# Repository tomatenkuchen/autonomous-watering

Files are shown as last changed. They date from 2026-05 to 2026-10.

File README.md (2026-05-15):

# autonomous-watering
esp32c6 based, solar powered, battery backuped garden water supply system

## todo
The objective of this project is to have an autonomous-as-can-be field water management system. it supports:
- [ ] multiple 24Vdc water valve connections for water distribution
- [ ] solar power supply to avoid grid wiring
- [ ] battery backup for valve power supply in case no sun is shining. watering is done best after heavy sun hours anyway
- [ ] wifi access point for watering configurations and updates
- [ ] optional conductivity sensor to measure earth humidity
- [ ] maybe maybe wifi powered wether data access to avoid watering just before the storm. GPS data relevant?
- [ ] bonus project: support for an electric fence to have sheep stay away from my salad

## Hardware

can be found in [this](./hw) folder. it's a [kicad](https://www.kicad.org) project, so no worries about licenses.
for now i plan to have an [ESP32C6] as the computing base.

## Software

is found in [this](./sw) folder. as it is an embedded project, it fits the hardware described in the [hardware folder](./hw).

## License

i intent to have the software and hardware licensed for GNU GPLv2. You will find either hardware part libraries or software libraries
licensed under different licenses (duh!), so please check the individual folders and references.

## Liabilities

this is my personal DIY project. It's supposed to be battery backed, so at least no grilling yourself on the grid issues to expected here.
nontheless, electrical danger lurks everywhere. Consider yourself to be warned! If you hurt yourself by soldering stuff, (mis-)handling batteries,
tripping over wires or get struck by lightning while setting up the system outside, blame yourself, not me.

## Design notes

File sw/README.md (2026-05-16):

# firmware for autonomous watering system

since hardware is using an esp32c6 as a controller and access interface for config and more, we need some code to flash onto it.

## usage

connect your pcb to your computer using a usb c cable.

to set up toolchain use:

```bash
pip install conan
conan config install https://github.com/tomatenkuchen/conan-settings.git
conan 

```

to build use:

```bash
source ~/my/path/to/esp-idf/export.sh
conan build . -pr=esp32c6 -b=missing
```

to flash use (after build):

```bash
conan export-pkg . -pr=esp32c6
```

## why conan

i know conan to be a useful package manager that has most of the software onboard that i need to use for my projects

## general structure

the device needs access to the following resources for the device to work properly:
- rtc for time keeping without network
- adc for earth conductivity measurement
- some gpios for valve switching

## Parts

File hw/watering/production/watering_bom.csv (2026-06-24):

Designator | Footprint | Quantity | Value | LCSC Part #
AE1 | Texas_SWRA117D_2.4GHz_Left | 1 | Antenna_Shield
BT1, BT2 | BH-18650-B1BA002 | 2 | 4V3 | C2988620
C1, C2 | 603 | 2 | 15p | C1644
C13, C14, C15, C16, C17, C18, C19, C20, C21, C24 | 603 | 10 | 1u | C15849
C26, C27, C28, C29, C30, C31, C32, C33, C34, C35, C36 | 1206 | 11 | 22u | C12891
C5, C6, C7 | 603 | 3 | 100n | C14663
D3 | TSOT-23 | 1 | D_TVS_Dual_AAC | C32677
D4, D5, D6, D7, D8 | D_SMA | 5 | SS210 | C14996
J2 | USB_C_Receptacle_GCT_USB4105-xx-A_16P_TopMnt_Horizontal | 1 | USB_C_Receptacle | C2927038
J3, J4, J6 | DB142R-5.08-2P-GN | 3 | Conn_01x02_Pin | C2898709
L10, L11, L13, L14, L8, L9 | L_Changjiang_FTC303020D | 6 | 22u | C18724424
Q1 | SOT-23 | 1 | 2N7002 | C8545
R1, R2 | 603 | 2 | 5k1 | C23186
R10, R14, R15, R17, R18, R20, R23, R24, R25, R28, R30, R31, R32, R35, R37, R38, R39, R43, R9 | 603 | 19 | 10k | C25804
R11, R29 | 603 | 2 | 47k | C25819
R12, R41, R42, R5 | 603 | 4 | 1k | C21190
R13, R21, R6 | 603 | 3 | 39k | C23153
R16, R22, R36 | 1206 | 3 | 0R1 | C25334
R19, R26, R40 | 603 | 3 | 100k | C25803
R27 | 603 | 1 | 220k | C22961
R33, R34 | 603 | 2 | 47 | C23182
SC1 | DB142R-5.08-2P-GN | 1 | Solar_Cell | C2898709
SW2, SW3 | SW_SPST_TS-1088-xR020 | 2 | KMS221GLFS | C720477
U1 | QFN-40-1EP_5x5mm_P0.4mm_EP3.6x3.6mm | 1 | ESP32-C6 | C5364646
U10, U8, U9 | SOIC-8_3.9x4.9mm_P1.27mm | 3 | MCP6002-xSN | C7377
U11, U4, U5, U6 | SOT-23-6 | 4 | STI3508 | C708881
U2 | WSON-8-1EP_2x2mm_P0.5mm_EP0.9x1.6mm | 1 | DRV8220DSG | C3681269
U3 | SOIC-8_5.3x5.3mm_P1.27mm | 1 | W25Q128JVS | C97521
U7 | WLCSP-4_0.64x0.64mm_Layout2x2_P0.35mm | 1 | NCP163AFCT330T2G | C603648
Y1 | Crystal_SMD_3225-4Pin_3.2x2.5mm | 1 | 40MHz | C9010
Y2 | Crystal_SMD_3215-2Pin_3.2x1.5mm | 1 | 32768Hz | C32346

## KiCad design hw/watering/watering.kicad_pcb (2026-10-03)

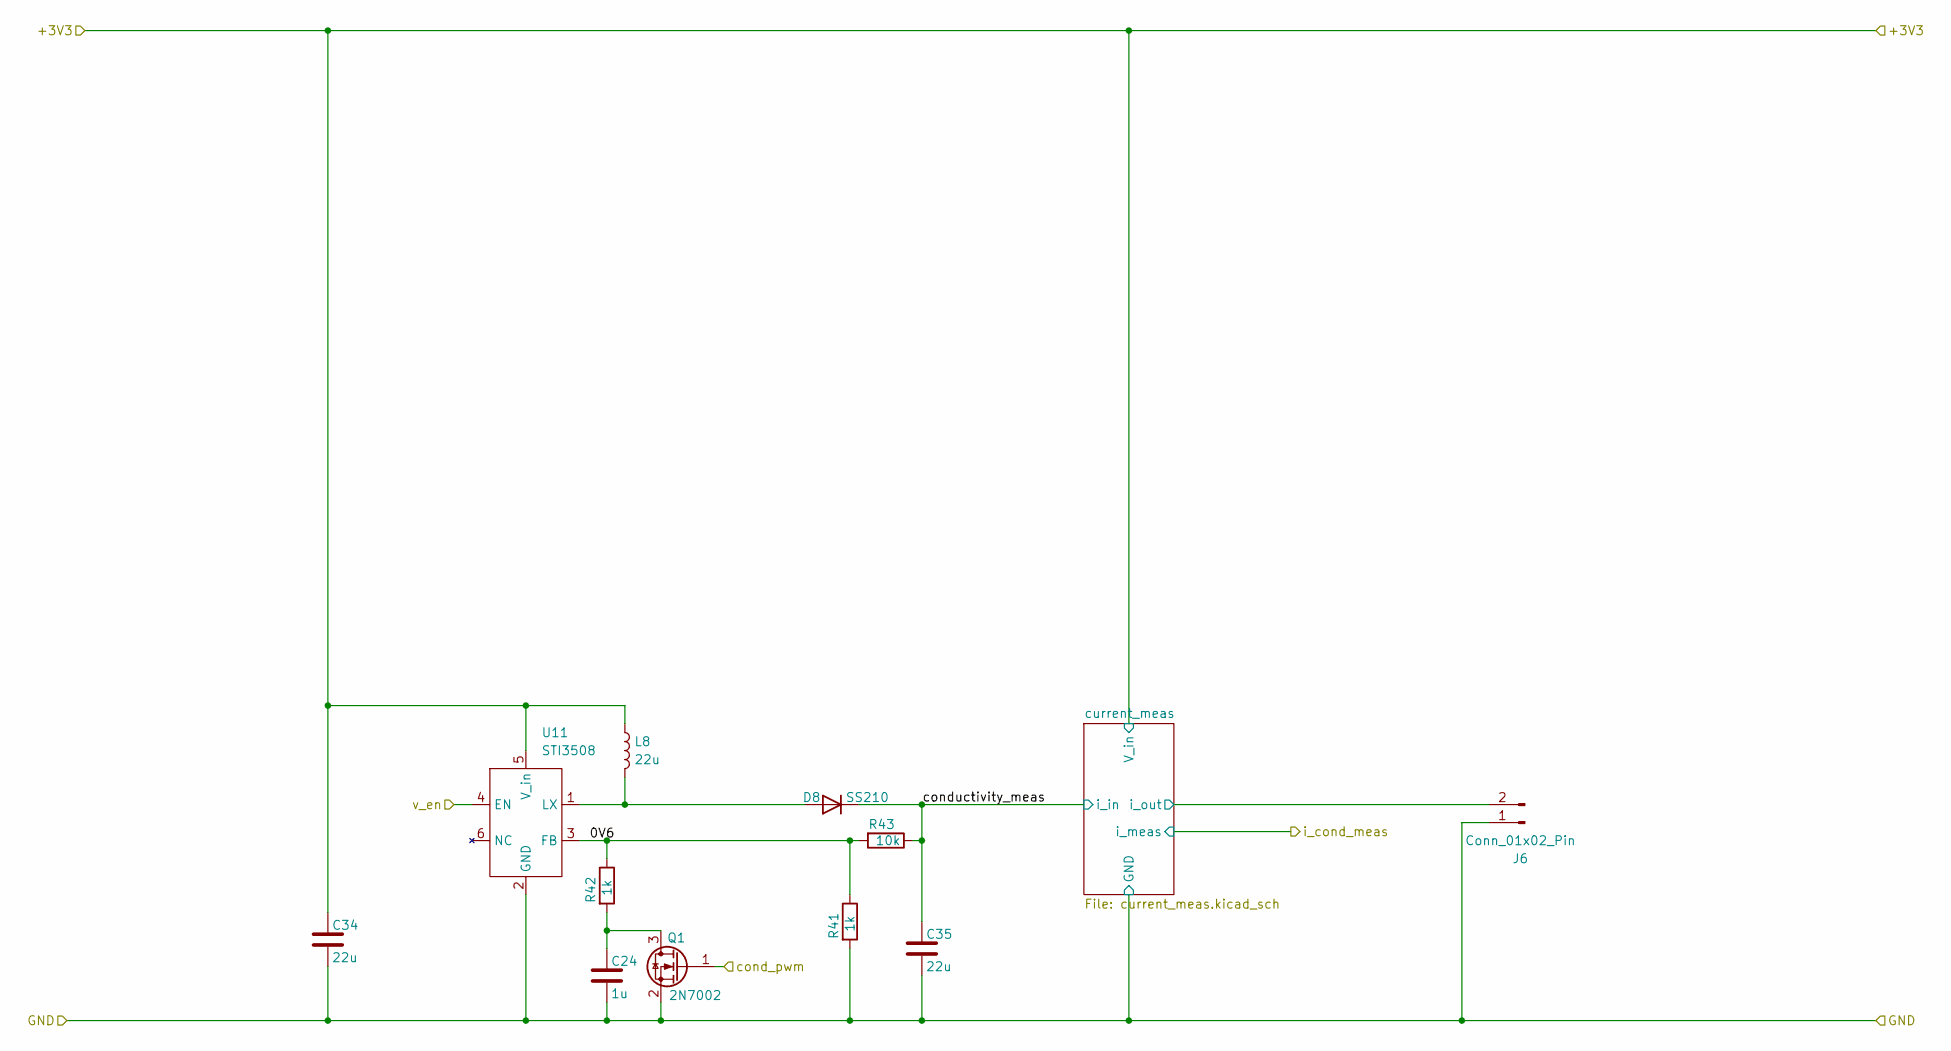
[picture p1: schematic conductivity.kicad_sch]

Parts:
C24: 1u; C_0603_1608Metric
C34, C35: 22u; C_1206_3216Metric
D8: SS210; D_SMA
J6: Conn_01x02_Pin; DB142R-5.08-2P-GN
L8: 22u; L_Changjiang_FTC303020D
Q1: 2N7002; SOT-23
R41, R42: 1k; R_0603_1608Metric
R43: 10k; R_0603_1608Metric
U11: STI3508; SOT-23-6

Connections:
/GND: C24.2, C34.2, C35.2, J6.1, Q1.2 (S), R41.2, U11.2 (GND); also elsewhere on the board
/V_bat: C34.1, L8.1, U11.5 (V_in); also elsewhere on the board
/conductivity/0V6: R41.1, R42.1, R43.2, U11.3 (FB)
/conductivity/cond_pwm: Q1.1 (G); also elsewhere on the board
/conductivity/conductivity_meas: C35.1, D8.1 (K), R43.1; also elsewhere on the board
/conductivity/current_meas/i_out: J6.2; also elsewhere on the board
/conductivity/v_en: U11.4 (EN); also elsewhere on the board
unnamed: D8.2 (A), L8.2, U11.1 (LX)
unnamed: C24.1, Q1.3 (D), R42.2

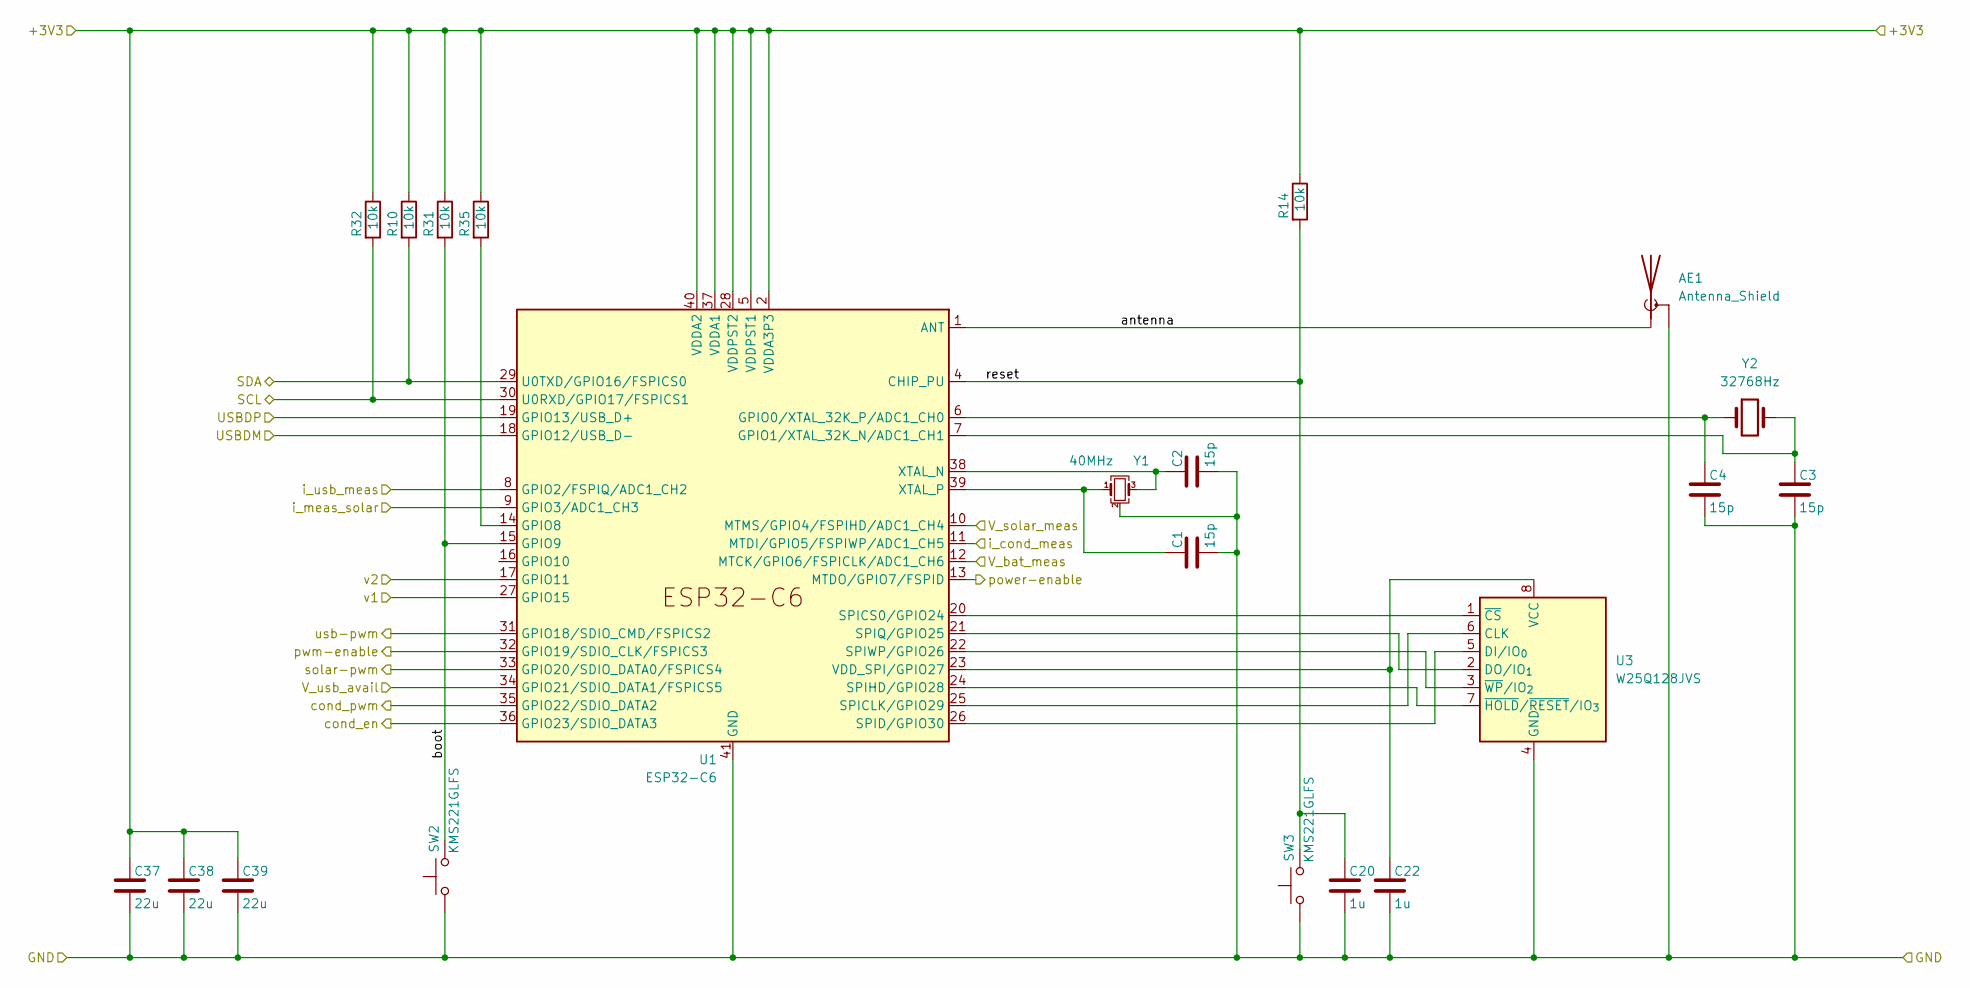
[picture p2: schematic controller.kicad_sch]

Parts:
AE1: Antenna_Shield; Texas_SWRA117D_2.4GHz_Left
C1, C2, C3, C4: 15p; C_0603_1608Metric
C20, C22: 1u; C_0603_1608Metric
C37, C38, C39: 22u; C_1206_3216Metric
R10, R14, R31, R32, R35: 10k; R_0603_1608Metric
SW2, SW3: KMS221GLFS; SW_SPST_TS-1088-xR020
U1: ESP32-C6; QFN-40-1EP_5x5mm_P0.4mm_EP3.6x3.6mm
U3: W25Q128JVS; SOIC-8_5.3x5.3mm_P1.27mm
Y1: 40MHz; Crystal_SMD_3225-4Pin_3.2x2.5mm
Y2: 32768Hz; Crystal_SMD_3215-2Pin_3.2x1.5mm

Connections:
/+3V3: C37.1, C38.1, C39.1, R10.1, R14.1, R31.1, R32.1, R35.1, U1.2 (VDDA3P3), U1.3 (VDDA3P3), U1.5 (VDDPST1), U1.28 (VDDPST2), U1.37 (VDDA1), U1.40 (VDDA2); also elsewhere on the board
/GND: AE1.2 (Shield), C1.2, C2.2, C3.2, C4.2, C20.2, C22.2, C37.2, C38.2, C39.2, SW2.1, SW3.1, U1.41 (GND), U3.4 (GND), Y1.2 (G), Y1.4 (G); also elsewhere on the board
/conductivity/cond_pwm: U1.35 (GPIO22/SDIO_DATA2); also elsewhere on the board
/conductivity/i_cond_meas: U1.11 (MTDI/GPIO5/FSPIWP/ADC1_CH5); also elsewhere on the board
/conductivity/v_en: U1.36 (GPIO23/SDIO_DATA3); also elsewhere on the board
/controller/SCL: R32.2, U1.30 (U0RXD/GPIO17/FSPICS1)
/controller/SDA: R10.2, U1.29 (U0TXD/GPIO16/FSPICS0)
/controller/USBDM: U1.18 (GPIO12/USB_D-); also elsewhere on the board
/controller/USBDP: U1.19 (GPIO13/USB_D+); also elsewhere on the board
/controller/V_bat_meas: U1.12 (MTCK/GPIO6/FSPICLK/ADC1_CH6); also elsewhere on the board
/controller/V_solar_meas: U1.10 (MTMS/GPIO4/FSPIHD/ADC1_CH4); also elsewhere on the board
/controller/V_usb_avail: U1.34 (GPIO21/SDIO_DATA1/FSPICS5); also elsewhere on the board
/controller/antenna: AE1.1 (A), U1.1 (ANT)
/controller/boot: R31.2, SW2.2, U1.15 (GPIO9)
/controller/i_meas_solar: U1.9 (GPIO3/ADC1_CH3); also elsewhere on the board
/controller/i_usb_meas: U1.8 (GPIO2/FSPIQ/ADC1_CH2); also elsewhere on the board
/controller/power-enable: U1.13 (MTDO/GPIO7/FSPID)
/controller/pwm-enable: U1.32 (GPIO19/SDIO_CLK/FSPICS3); also elsewhere on the board
/controller/reset: C20.1, R14.2, SW3.2, U1.4 (CHIP_PU)
/controller/solar-pwm: U1.33 (GPIO20/SDIO_DATA0/FSPICS4); also elsewhere on the board
/controller/usb-pwm: U1.31 (GPIO18/SDIO_CMD/FSPICS2); also elsewhere on the board
/controller/v1: U1.27 (GPIO15); also elsewhere on the board
/controller/v2: U1.17 (GPIO11); also elsewhere on the board
unnamed: C4.1, U1.6 (GPIO0/XTAL_32K_P/ADC1_CH0), Y2.1
unnamed: C3.1, U1.7 (GPIO1/XTAL_32K_N/ADC1_CH1), Y2.2
unnamed: R35.2, U1.14 (GPIO8)
unnamed: U1.25 (SPICLK/GPIO29), U3.6 (CLK)
unnamed: U1.20 (SPICS0/GPIO24), U3.1 (~CS)
unnamed: U1.26 (SPID/GPIO30), U3.5 (DI/IO_{0})
unnamed: U1.24 (SPIHD/GPIO28), U3.7 (~HOLD/~RESET/IO_{3})
unnamed: U1.21 (SPIQ/GPIO25), U3.2 (DO/IO_{1})
unnamed: U1.22 (SPIWP/GPIO26), U3.3 (~WP/IO_{2})
unnamed: C22.1, U1.23 (VDD_SPI/GPIO27), U3.8 (VCC)
unnamed: C2.1, U1.38 (XTAL_N), Y1.3
unnamed: C1.1, U1.39 (XTAL_P), Y1.1

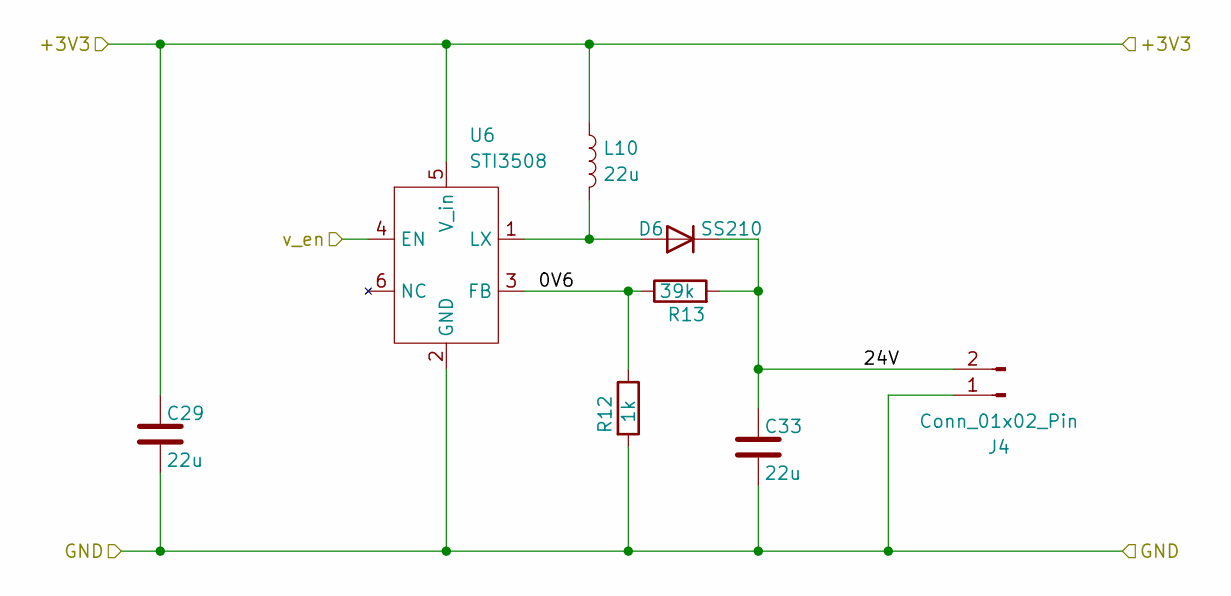
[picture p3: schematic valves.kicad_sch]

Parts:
C29, C33: 22u; C_1206_3216Metric
D6: SS210; D_SMA
J4: Conn_01x02_Pin; DB142R-5.08-2P-GN
L10: 22u; L_Changjiang_FTC303020D
R12: 1k; R_0603_1608Metric
R13: 39k; R_0603_1608Metric
U6: STI3508; SOT-23-6

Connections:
/GND: C29.2, C33.2, J4.1, R12.2, U6.2 (GND); also elsewhere on the board
/V_bat: C29.1, L10.1, U6.5 (V_in); also elsewhere on the board
/controller/v2: U6.4 (EN); also elsewhere on the board
/valves2/0V6: R12.1, R13.1, U6.3 (FB)
/valves2/24V: C33.1, D6.1 (K), J4.2, R13.2
unnamed: D6.2 (A), L10.2, U6.1 (LX)

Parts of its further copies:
C28, C30: 22u; C_1206_3216Metric
D7: SS210; D_SMA
J3: Conn_01x02_Pin; DB142R-5.08-2P-GN
L11: 22u; L_Changjiang_FTC303020D
R5: 1k; R_0603_1608Metric
R6: 39k; R_0603_1608Metric
U4: STI3508; SOT-23-6

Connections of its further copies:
/GND: C28.2, C30.2, J3.1, R5.2, U4.2 (GND); also elsewhere on the board
/V_bat: C28.1, L11.1, U4.5 (V_in); also elsewhere on the board
/controller/v1: U4.4 (EN); also elsewhere on the board
/valves1/0V6: R5.1, R6.1, U4.3 (FB)
/valves1/24V: C30.1, D7.1 (K), J3.2, R6.2
unnamed: D7.2 (A), L11.2, U4.1 (LX)

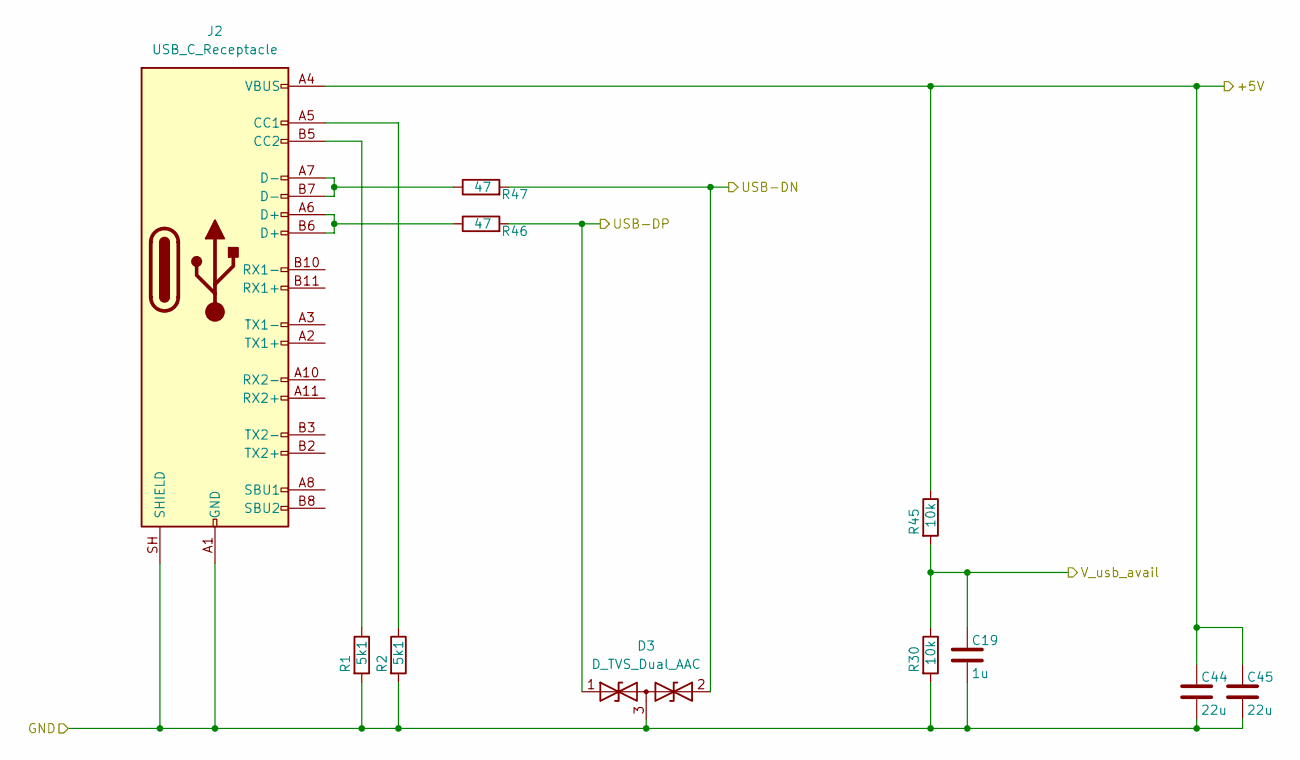
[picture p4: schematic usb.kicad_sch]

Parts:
C19: 1u; C_0603_1608Metric
C44, C45: 22u; C_1206_3216Metric
D3: D_TVS_Dual_AAC; TSOT-23
J2: USB_C_Receptacle; USB_C_Receptacle_GCT_USB4105-xx-A_16P_TopMnt_Horizontal
R1, R2: 5k1; R_0603_1608Metric
R30, R45: 10k; R_0603_1608Metric
R46, R47: 47; R_0603_1608Metric

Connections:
/+5V: C44.1, C45.1, J2.A4 (VBUS), J2.A9 (VBUS), J2.B4 (VBUS), J2.B9 (VBUS), R45.1; also elsewhere on the board
/GND: C19.2, C44.2, C45.2, D3.3 (common), J2.A1 (GND), J2.A12 (GND), J2.B1 (GND), J2.B12 (GND), J2.SH (SHIELD), R1.2, R2.2, R30.2; also elsewhere on the board
/controller/USBDM: D3.2 (A2), R47.2; also elsewhere on the board
/controller/USBDP: D3.1 (A1), R46.2; also elsewhere on the board
/controller/V_usb_avail: C19.1, R30.1, R45.2; also elsewhere on the board
unnamed: J2.A5 (CC1), R2.1
unnamed: J2.B5 (CC2), R1.1
unnamed: J2.A6 (D+), J2.B6 (D+), R46.1
unnamed: J2.A7 (D-), J2.B7 (D-), R47.1

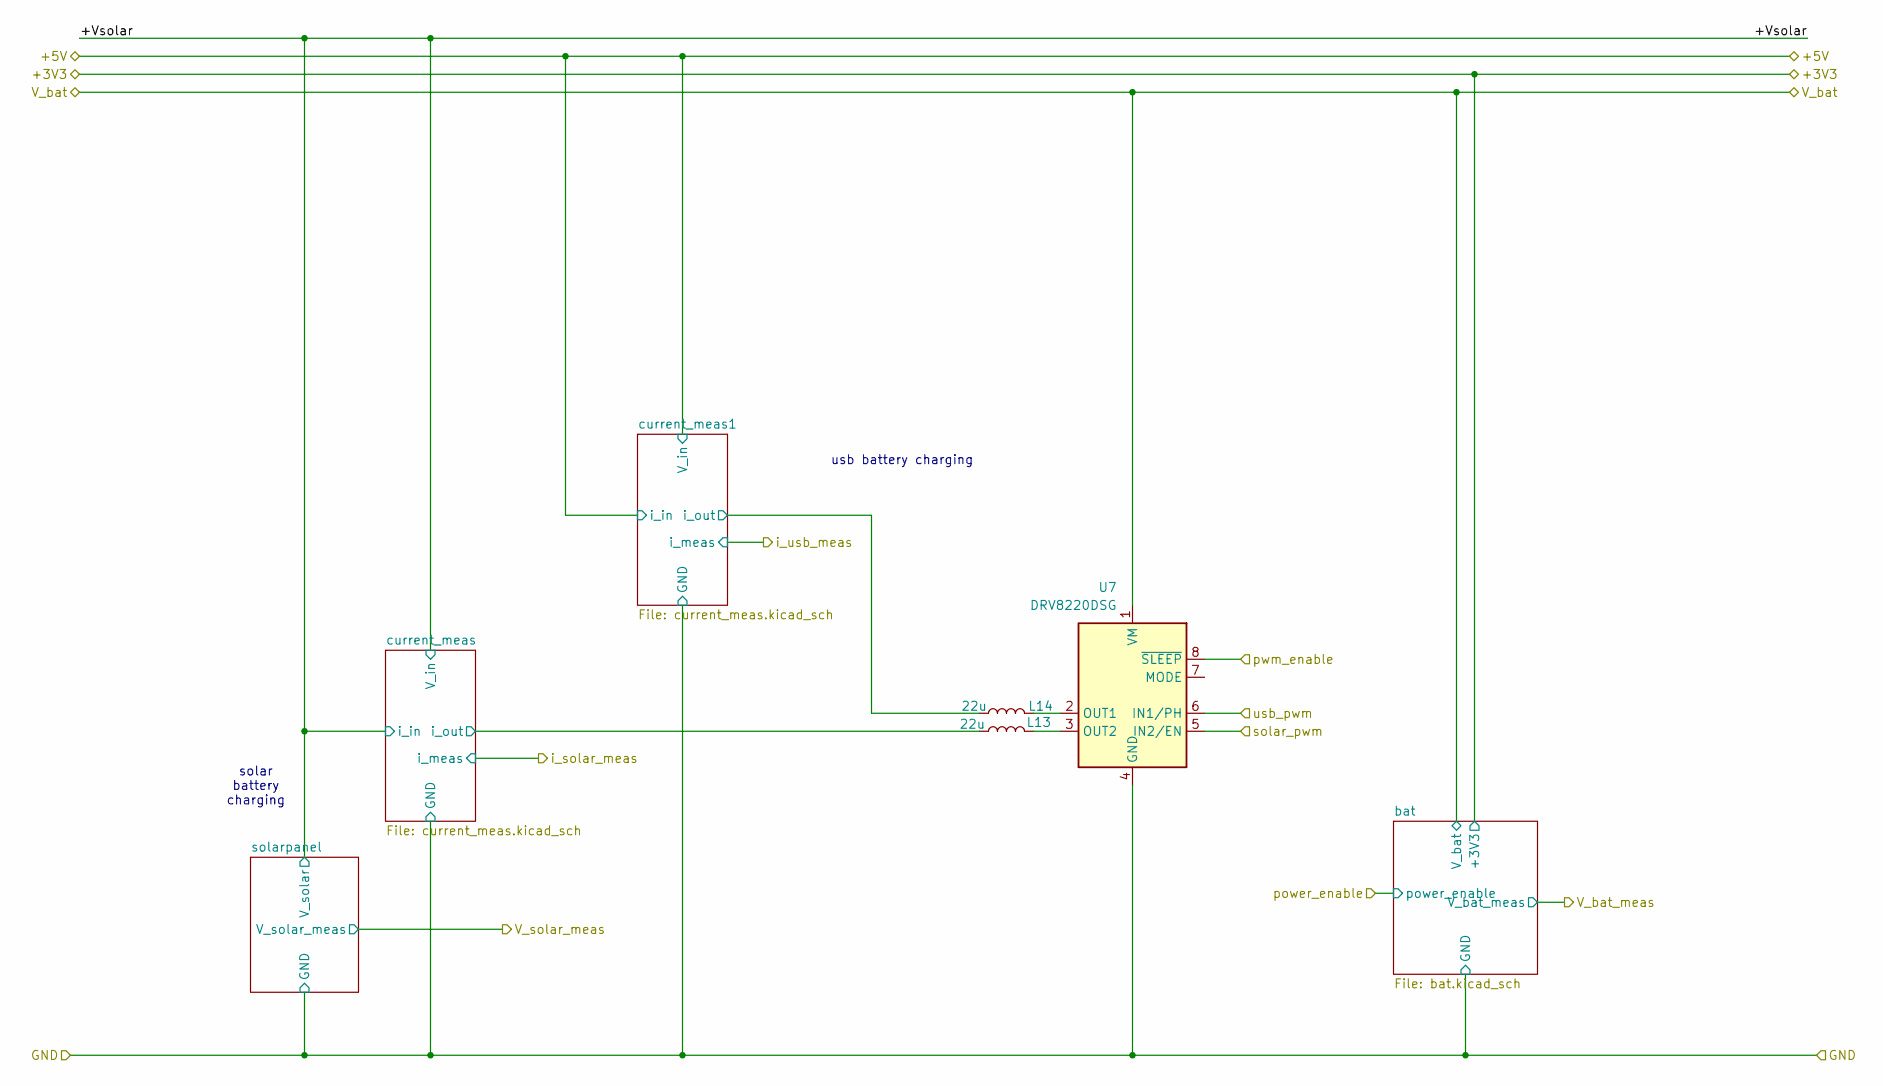
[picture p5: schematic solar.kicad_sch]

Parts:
L13, L14: 22u; L_Changjiang_FTC303020D
U7: DRV8220DSG; Texas_DSG0008A_WSON-8-1EP_2x2mm_P0.5mm_EP0.9x1.6mm

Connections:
/GND: U7.4 (GND), U7.9 (GND); also elsewhere on the board
/V_bat: U7.1 (VM); also elsewhere on the board
/controller/pwm-enable: U7.8 (~SLEEP); also elsewhere on the board
/controller/solar-pwm: U7.5 (IN2/EN); also elsewhere on the board
/controller/usb-pwm: U7.6 (IN1/PH); also elsewhere on the board
/solar/current_meas1/i_out: L14.2; also elsewhere on the board
/solar/current_meas/i_out: L13.2; also elsewhere on the board
unnamed: L14.1, U7.2 (OUT1)
unnamed: L13.1, U7.3 (OUT2)

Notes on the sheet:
usb battery charging
solar battery charging

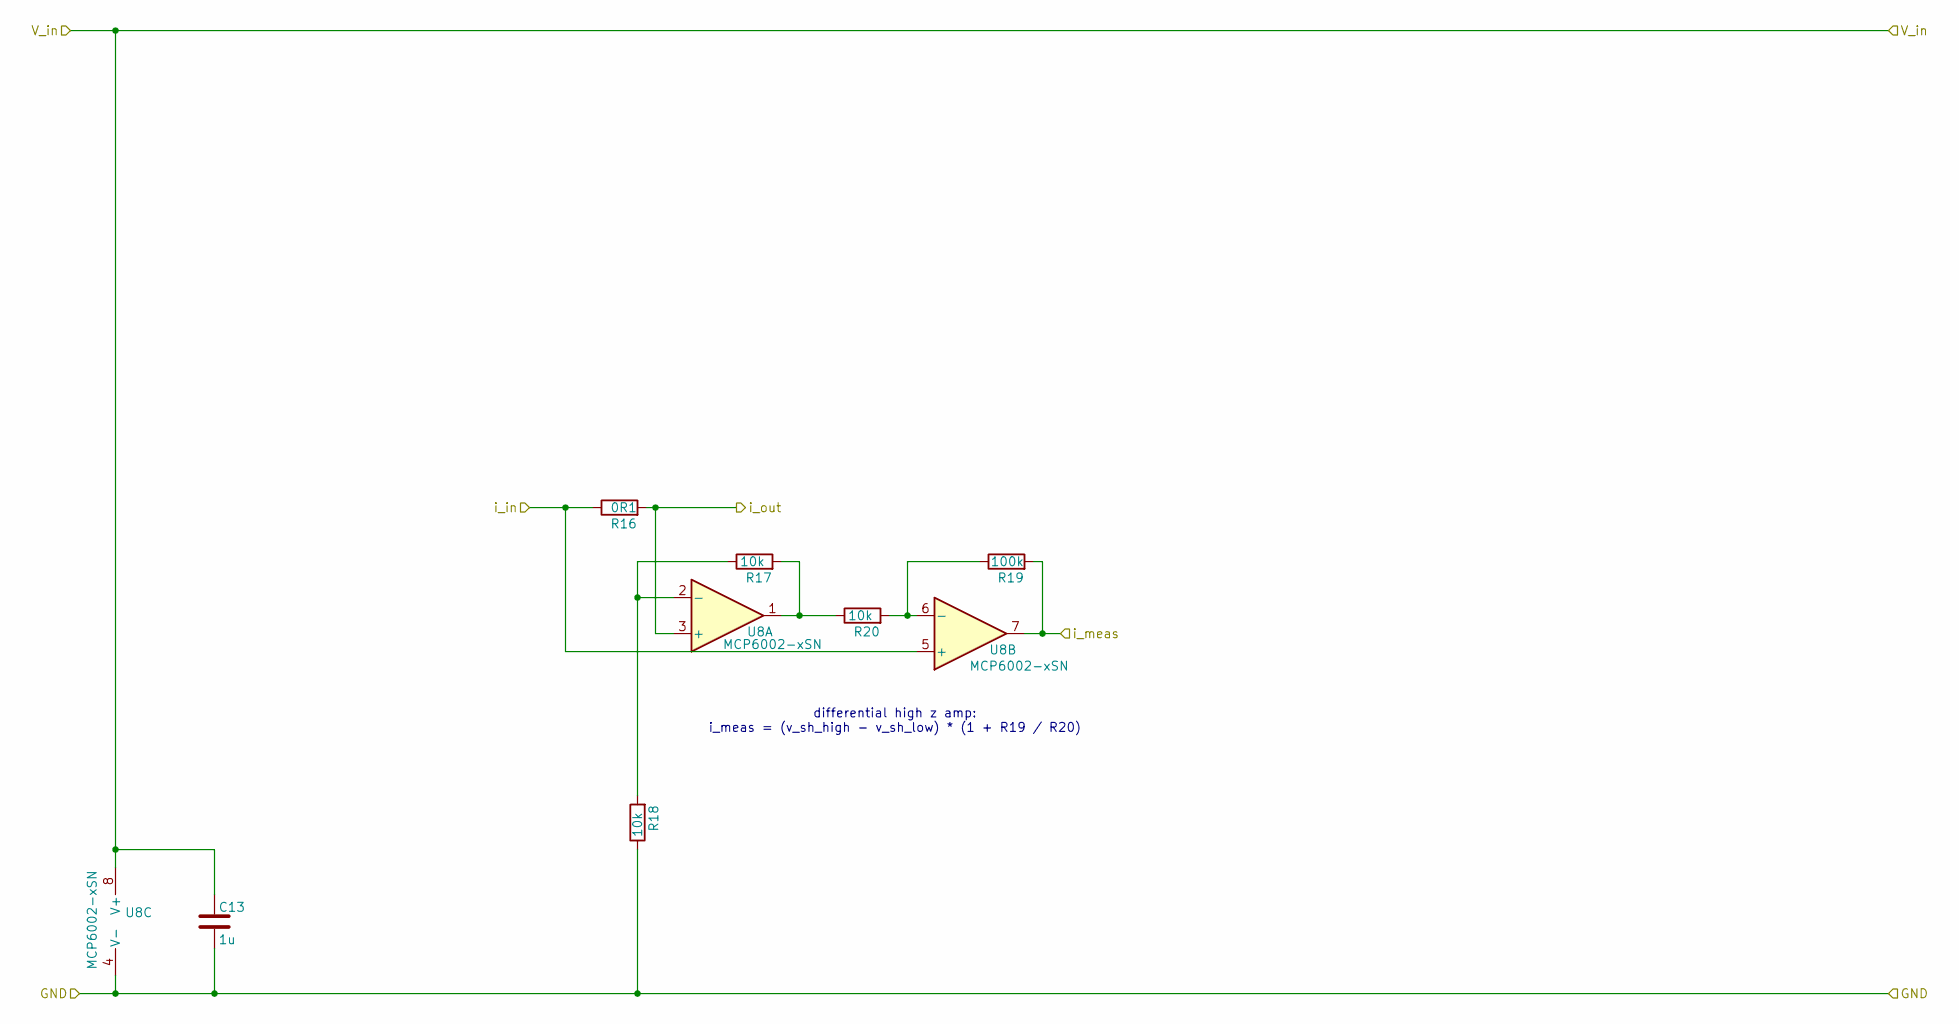
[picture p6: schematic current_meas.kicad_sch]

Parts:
C13: 1u; C_0603_1608Metric
R16: 0R1; R_1206_3216Metric
R17, R18, R20: 10k; R_0603_1608Metric
R19: 100k; R_0603_1608Metric
U8: MCP6002-xSN; SOIC-8_3.9x4.9mm_P1.27mm

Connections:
/GND: C13.2, R18.1, U8.4 (V-); also elsewhere on the board
/controller/i_meas_solar: R19.2, U8.7; also elsewhere on the board
/solar/+Vsolar: C13.1, R16.1, U8.5 (+), U8.8 (V+); also elsewhere on the board
/solar/current_meas/i_out: R16.2, U8.3 (+); also elsewhere on the board
unnamed: R17.2, R20.1, U8.1
unnamed: R17.1, R18.2, U8.2 (-)
unnamed: R19.1, R20.2, U8.6 (-)

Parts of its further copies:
C14, C21: 1u; C_0603_1608Metric
R22, R36: 0R1; R_1206_3216Metric
R23, R24, R25, R37, R38, R39: 10k; R_0603_1608Metric
R26, R40: 100k; R_0603_1608Metric
U9, U10: MCP6002-xSN; SOIC-8_3.9x4.9mm_P1.27mm

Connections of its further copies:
/+5V: C14.1, R22.1, U9.5 (+), U9.8 (V+); also elsewhere on the board
/GND: C14.2, C21.2, R23.1, R37.1, U9.4 (V-), U10.4 (V-); also elsewhere on the board
/V_bat: C21.1, U10.8 (V+); also elsewhere on the board
/conductivity/conductivity_meas: R36.1, U10.5 (+); also elsewhere on the board
/conductivity/current_meas/i_out: R36.2, U10.3 (+); also elsewhere on the board
/conductivity/i_cond_meas: R40.2, U10.7; also elsewhere on the board
/controller/i_usb_meas: R26.2, U9.7; also elsewhere on the board
/solar/current_meas1/i_out: R22.2, U9.3 (+); also elsewhere on the board
unnamed: R24.2, R25.1, U9.1
unnamed: R38.2, R39.1, U10.1
unnamed: R23.2, R24.1, U9.2 (-)
unnamed: R25.2, R26.1, U9.6 (-)
unnamed: R37.2, R38.1, U10.2 (-)
unnamed: R39.2, R40.1, U10.6 (-)

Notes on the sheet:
differential high z amp: i_meas = (v_sh_high - v_sh_low) * (1 + R19 / R20)

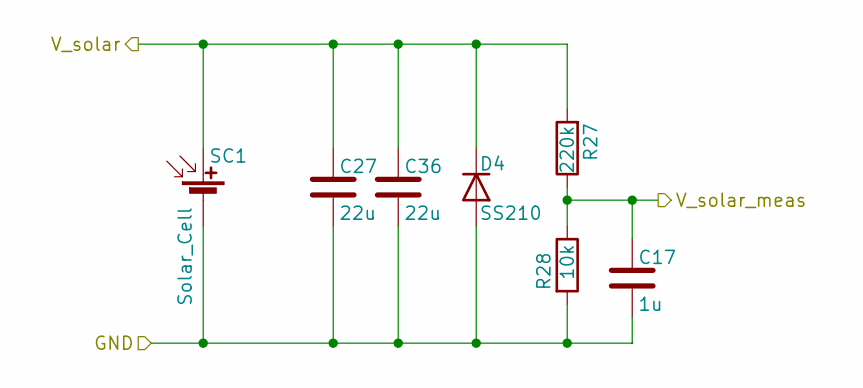
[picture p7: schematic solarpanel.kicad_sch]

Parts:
C17: 1u; C_0603_1608Metric
C27, C36: 22u; C_1206_3216Metric
D4: SS210; D_SMA
R27: 220k; R_0603_1608Metric
R28: 10k; R_0603_1608Metric
SC1: Solar_Cell; DB142R-5.08-2P-GN

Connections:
/GND: C17.2, C27.2, C36.2, D4.2 (A), R28.2, SC1.2 (-); also elsewhere on the board
/controller/V_solar_meas: C17.1, R27.1, R28.1; also elsewhere on the board
/solar/+Vsolar: C27.1, C36.1, D4.1 (K), R27.2, SC1.1 (+); also elsewhere on the board

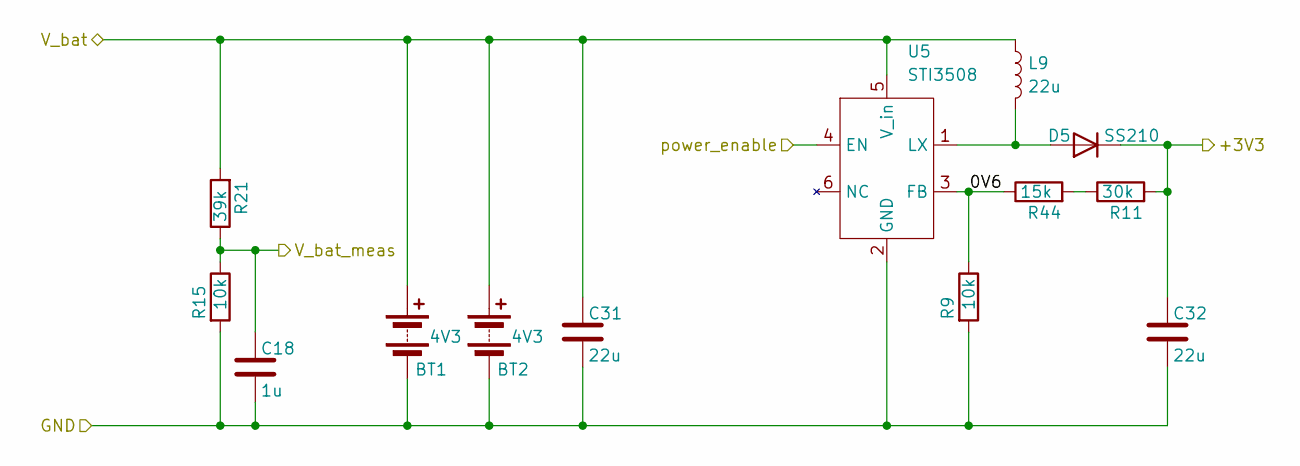
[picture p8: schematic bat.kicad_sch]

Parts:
BT1, BT2: 4V3; BH-18650-B1BA002
C18: 1u; C_0603_1608Metric
C31, C32: 22u; C_1206_3216Metric
D5: SS210; D_SMA
L9: 22u; L_Changjiang_FTC303020D
R9, R15: 10k; R_0603_1608Metric
R11: 30k; R_0603_1608Metric
R21: 39k; R_0603_1608Metric
R44: 15k; R_0603_1608Metric
U5: STI3508; SOT-23-6

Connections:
/+3V3: C32.1, D5.1 (K), R11.2; also elsewhere on the board
/GND: BT1.2 (-), BT2.2 (-), C18.2, C31.2, C32.2, R9.2, R15.2, U5.2 (GND); also elsewhere on the board
/V_bat: BT1.1 (+), BT2.1 (+), C31.1, L9.1, R21.2, U5.5 (V_in); also elsewhere on the board
/controller/V_bat_meas: C18.1, R15.1, R21.1; also elsewhere on the board
/solar/bat/0V6: R9.1, R44.1, U5.3 (FB)
/solar/power_enable: U5.4 (EN)
unnamed: D5.2 (A), L9.2, U5.1 (LX)
unnamed: R11.1, R44.2

Board: 2 copper layers, 103 parts (2 on the bottom side), 68 nets, no tracks yet.

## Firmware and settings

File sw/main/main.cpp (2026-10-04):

/**
 * @file main.cpp
 * @brief entry point of executable
 */

#include "adc.hpp"
#include "credentials.hpp"
#include "driver/temperature_sensor.h"
#include "esp_log.h"
#include "freertos.hpp"
#include "power.hpp"
#include "server.hpp"
#include "valves.hpp"
#include <chrono>

using namespace std::chrono_literals;

namespace {

const static char *TAG = "main";

temperature_sensor_handle_t temp_sensor = nullptr;

// Initialize Built-in Temperature Sensor
auto init_temp_sensor() -> void {
  temperature_sensor_config_t temp_cfg =
      TEMPERATURE_SENSOR_CONFIG_DEFAULT(20, 50);
  ESP_ERROR_CHECK(temperature_sensor_install(&temp_cfg, &temp_sensor));
  ESP_ERROR_CHECK(temperature_sensor_enable(temp_sensor));
}

} // namespace

extern "C" void app_main() {
  init_temp_sensor();

  bsp::Power power;

  mqtt_server::Iface iface{
      .get_temperature_celsius =
          [] {
            float t;
            temperature_sensor_get_celsius(temp_sensor, &t);
            return t;
          },
      .get_battery_voltage_mV =
          [&power] {
            return power.get_voltage_mV(bsp::Power::AdcInputs::v_battery);
          },
  };

  mqtt_server::start(credentials::server_config, credentials::wifi_credentials,
                     iface);

  while (true) {
    // power transfer to battery
    power.set_solar_current_ref_mA(1);

    freertos::delay(10s);
  }
}

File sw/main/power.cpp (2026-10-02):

#include "power.hpp"
#include "adc.hpp"
#include "driver/gpio.h"
#include "esp_log.h"
#include <algorithm>
#include <array>
#include <cstdint>

namespace {
const static char *TAG = "power";
}

namespace bsp {

Power::Power() : adc(ADC_UNIT_1, adc_channels) {
  ESP_LOGI(TAG, "power object constructed");
}

auto Power::get_voltage_mV(AdcInputs input) -> std::uint16_t {
  switch (input) {
  case AdcInputs::v_solar: {
    float const R1 = 220'000.0f;
    float const R2 = 10'000.0f;
    auto const v_solar_meas_mV = adc.get_voltage_mV((int)v_solar);
    auto const v_solar_mV = v_solar_meas_mV * (R1 + R2) / R2;
    return static_cast<uint16_t>(v_solar_mV);
  }
  case AdcInputs::v_battery: {
    float const R1 = 39'000.0f;
    float const R2 = 10'000.0f;
    auto const v_battery_meas_mV = adc.get_voltage_mV((int)v_battery);
    auto const v_battery_mV = v_battery_meas_mV * (R1 + R2) / R2;
    return static_cast<uint16_t>(v_battery_mV);
  }
  case AdcInputs::i_conductivity:
  case AdcInputs::i_usb:
  case AdcInputs::i_solar:
  default:
    return 0;
  }
}

auto Power::get_current_mA(AdcInputs input) -> std::uint16_t {
  float const R_sh = 0.1f;
  float amp = 11.0f;
  auto const V_meas_mV = adc.get_voltage_mV((int)input);
  auto const V_sh_mV = V_meas_mV / amp;
  auto const I_sh_mA = V_sh_mV / R_sh;
  return static_cast<std::uint16_t>(I_sh_mA);
}

auto Power::set_conductivity_voltage_mV(std::uint16_t output_mV) -> void {
  std::uint16_t const V_max_mV = 24'000;
  // limit
  auto const V_out_mV = std::min(V_max_mV, output_mV);

  auto const duty = V_out_mV * 65535UL / V_max_mV;

  pwm.set_conductivity_duty(duty);
}

auto Power::is_usb_voltage_online() -> bool {
  gpio_config_t v_usb_gpio = {
      .pin_bit_mask = 1 << 21,
      .mode = GPIO_MODE_INPUT,
      .pull_up_en = GPIO_PULLUP_DISABLE,
      .pull_down_en = GPIO_PULLDOWN_ENABLE,
      .intr_type = GPIO_INTR_DISABLE,
  };
  ESP_ERROR_CHECK(gpio_config(&v_usb_gpio));
  return gpio_get_level(GPIO_NUM_21) == 1;
}

auto Power::set_usb_current_ref_mA(std::int32_t current_mA) -> void {
  if (current_mA < 0) {
    current_mA = 0;
  }

  if (current_mA == 0) {
    pwm.enable(false);
    return;
  }

  pwm.enable(true);

  auto const i_usb_mA = get_current_mA(AdcInputs::i_usb);
  auto const error_mA = current_mA - i_usb_mA;
  // update PID controller with the error
  auto const pid_usb_duty = pid_usb.update(error_mA);

  ESP_LOGI(TAG, "current_mA: %d, i_usb_mA: %d, error_mA: %d, pid_usb_duty: %f",
           current_mA, i_usb_mA, error_mA, pid_usb_duty);

  // controller here
}

auto Power::set_solar_current_ref_mA(std::int32_t current_mA) -> void {
  if (current_mA < 0) {
    current_mA = 0;
  }
  if (current_mA == 0) {
    pwm.enable(false);
    return;
  }
  auto const cell_voltage_mV = get_voltage_mV(AdcInputs::v_battery);

  if (cell_voltage_mV > 4'300) {
    ESP_LOGW(TAG, "solar voltage too high: %d mV", cell_voltage_mV);
    pwm.enable(false);
    return;
  }

  ESP_LOGI(TAG, "battery voltage: %d mV", cell_voltage_mV);

  pwm.enable(true);
  // controller here
  auto const d = 62'000;
  pwm.set_solar_duty(d);
  pwm.set_usb_duty(d);
}

} // namespace bsp

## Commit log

2026-05-16 adc bsp package
    [watering.kicad_pcb, watering.kicad_sch]
2026-05-17 changed chip to esp32c6
2026-05-17 - changed clangformat for constructor initializations to be always newlined - adaptation of adc class to esp32c6 - adaptation of channel definition to xiao esp32c6 module
2026-05-27 added esp32c6
    [watering.kicad_sch]
2026-05-27 added battery management chip
    [controller.kicad_sch, solar.kicad_sch, valves.kicad_sch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]
2026-05-30 added supply chip for battery and solar
    [controller.kicad_sch, solar.kicad_sch, valves.kicad_sch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]
2026-06-04 updated power
    [controller.kicad_sch, solar.kicad_sch, valves.kicad_sch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]
2026-06-04 hardware progres
    [solar.kicad_sch, valves.kicad_sch, watering.kicad_pcb]
2026-06-06 some progress on energy harvesting
    [current_meas.kicad_sch, ldo.kicad_sch, solar.kicad_sch]
2026-06-07 connections completet. started placing and routing
    [controller.kicad_sch, current_meas.kicad_sch, ldo.kicad_sch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]
2026-06-08 some more placing
    [controller.kicad_sch, solar.kicad_sch, watering.kicad_pcb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]
2026-06-10 routing done
    [conductivity.kicad_sch, controller.kicad_sch, current_meas.kicad_sch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]
2026-06-10 - updated parts numbers - created jlc outputs
    [conductivity.kicad_sch, solar.kicad_sch, watering.kicad_pcb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]
2026-06-13 updated switches
    [controller.kicad_sch, watering.kicad_pcb, watering_bom.csv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]
2026-06-13 updated bom
    [watering_bom.csv]
2026-06-15 updated inductors
    [conductivity.kicad_sch, solar.kicad_sch, valves.kicad_sch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]
2026-06-24 more usb compliance
    [watering.kicad_pcb, watering.kicad_sch]
2026-06-24 - updated bom - updated dorabo connector footprint - added some stitching vias
    [watering.kicad_pcb, watering.kicad_sch, watering_bom.csv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]
2026-06-24 - added naming to adc inputs - added pwm class
2026-06-24 some more pwm and valves
